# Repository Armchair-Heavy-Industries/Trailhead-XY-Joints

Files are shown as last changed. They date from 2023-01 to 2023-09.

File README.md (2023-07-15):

# Trailhead-XY-Joints
Modified XY joints for the Voron 2.4 and Trident

Project Leads: Corvid and Derpimus

Join me on Discord (https://discord.gg/armchairengineeringsux)
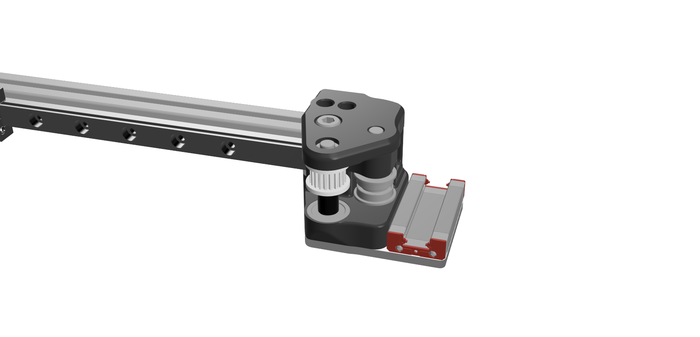
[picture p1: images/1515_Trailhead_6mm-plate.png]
Render

## Note
Consider these files as a beta.

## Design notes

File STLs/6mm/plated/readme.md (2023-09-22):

# Plated 2020 Trailhead assembly

## Bill of materials

| Amount | Part |
| --- | ---- |
| 8 | F695 bearing |
| 2 | De-hubbed pulley or toothed idler |
| 4 | 5x7x1mm shim |
| 4 | 5x35mm G6 steel pins |
| 4 | M3 heatset insert |
| 4 | M5x10 BHCS |
| 2 | M5x35 SHCS |
| 8 | M3x6 BHCS |
| 2 | M3x12 BHCS |
| 4 | M3x16 BHCS |

> [!NOTE]
> It might be useful to design and print spacers between then toothed idler/dehubbed pulley to ensure that the F695 bearings stay in place.

## Assembly view

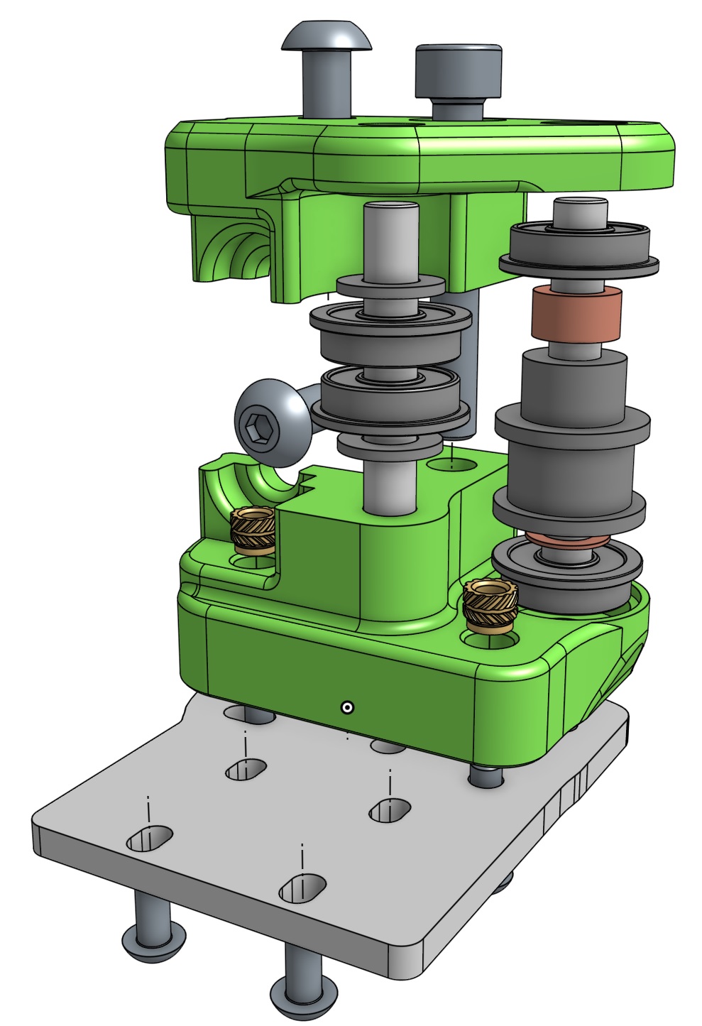
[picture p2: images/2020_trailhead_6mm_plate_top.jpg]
Top perspective


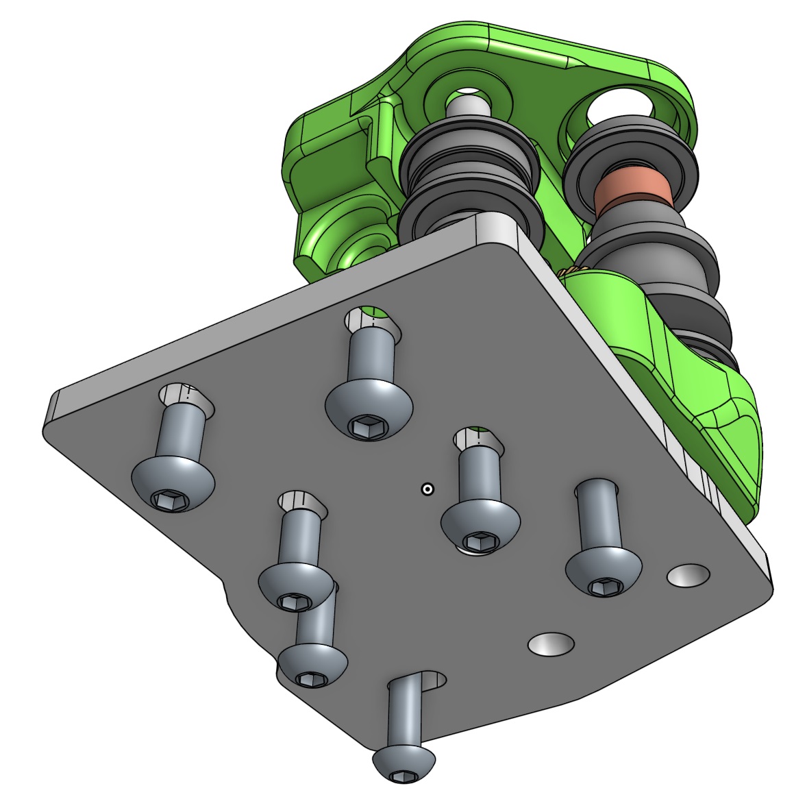
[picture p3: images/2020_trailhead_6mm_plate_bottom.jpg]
Bottom perspective


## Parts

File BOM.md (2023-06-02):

# Bill of Materials

## Plated, 1515 Extrusion, 6mm Belts

### Source:
- 2x cut aluminum plates, 0.125" / 3.2mm thick, using DXF/xyjplate[x2].dxf
- (optional) 1x cut titanium plate, 0.125" / 3.2mm thick, using DXF/1515_x_backer_(size).DXF
- 1515 profile extrusion, e.g. [from Misumi](https://us.misumi-ec.com/vona2/detail/110300465870/)
    - Length is the X-axis extrusion, e.g. 300mm spec Trident uses 380mm extrusion
- M3 tap to use on the extrusion ends

### Print: 
- xyj-left-lower-plated.stl
- xyj-right-lower-plated.stl
- 1515 6mm Trailhead - XY Joint - Left Top.stl
- 1515 6mm Trailhead - XY Joint - Right Top.stl
- 2x misumi1515nodropsquare6mm.stl
- 27x misumi1515nodropsquare.stl (You may have leftovers)

### Small Parts:
- 4x M3 heatset inserts
    - Insert into xyj-*-lower-plated printed parts
- 2x 6mm pulley for belts
- 8x F695 bearing (Four greater than the stock XY joints)
- 27x Roll/Slide-in M3 T-nuts for 1515 Extrusions
    - choose the correct type for your 1515 profile. LDO and Makerbeam are different.
- 29x M3x6mm BHCS
    - 2x through rear of extrusion
    - 10x through X-axis MGN rail (for 300mm spec / 350mm rail / 380mm extrusion)
    - (optional) 9x through titanium backer bar
    - 8x through plates into Y axis MGN carriage
- 4x M3x8mm SHCS
    - 4x through upper printed joints into extrusion
- 4x M3x12mm SHCS
    - 2x through plate, into heatset in lower printed joint
    - 2x into extrusion end
- 2x M3x16mm SHCS
    - 2x through plate, into heatset in lower printed joint
- 2x M3x20mm SHCS
    - 2x through plate, through lower printed joint, into extrusion
- 8x M3 washer
    - 2x for the M3x12 SHCS into the ends of the extrusion
    - 6x for the M3 SHCS screws through bottom of the plates
    - No washers for the M3x6 BHCS screws that go into the carriages
- 2x M5x40mm SHCS
    - 2x through entire XY joint from top to bottom.
- 2x M5 washer
    - 2x between plate and nut
- 2x M5 nut
    - Secure the M5x40mm SHCS at the bottom of each plate. Tighten with a wrench + pliers
- 4x 5mm x 35mm shafts (These are different from the 40mm shafts used in the regular pins mod!)

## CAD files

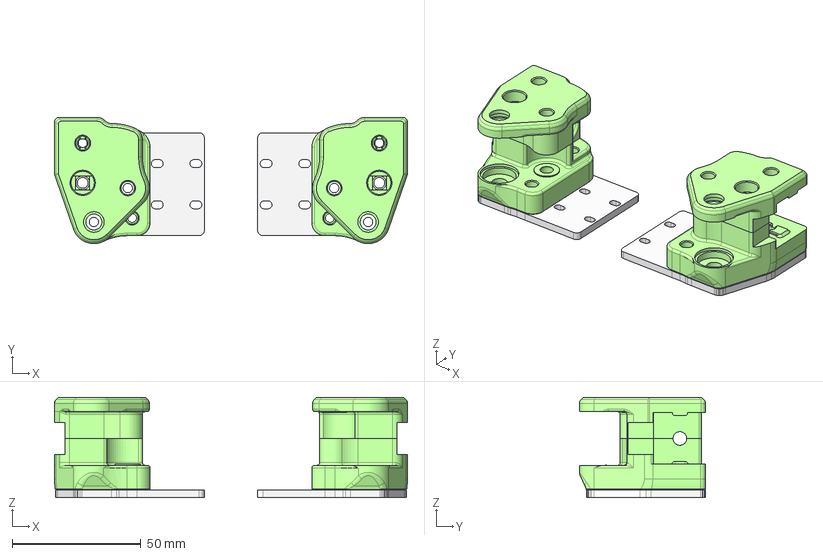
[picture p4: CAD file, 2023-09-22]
CAD/2020_Trailhead_6mm-plate.step
137.1 x 49.0 x 39.0 mm
XY Joint Left Bottom R3
Trailhead Plate x 2
XY Joint Right Bottom R3
XY Joint Left Top R3
XY Joint Right Top R3

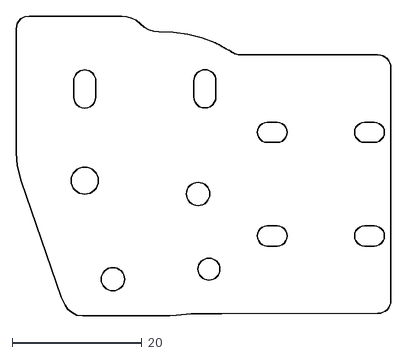
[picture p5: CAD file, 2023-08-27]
DXF/trailhead_plate[x2].dxf
57.8 x 46.3

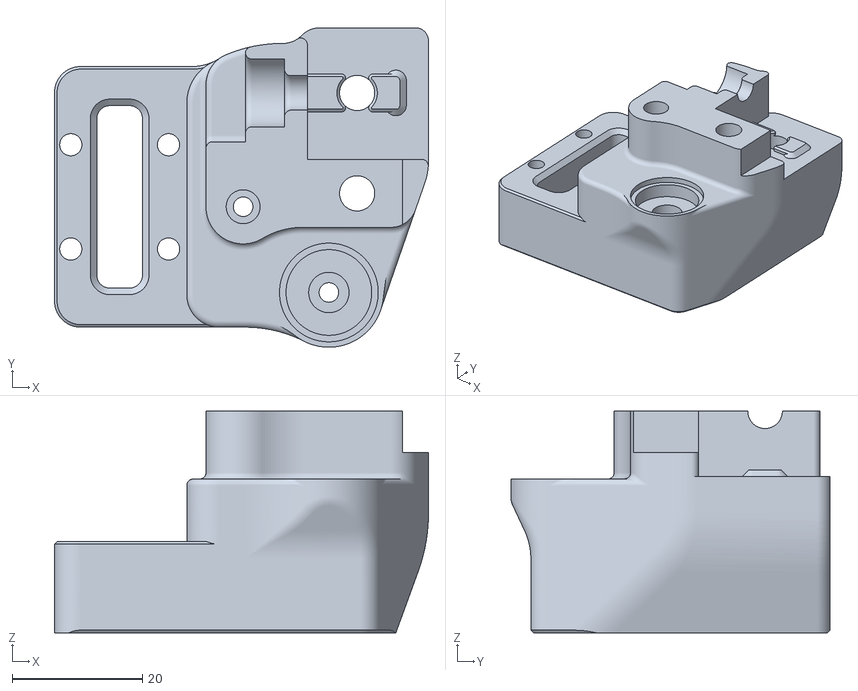
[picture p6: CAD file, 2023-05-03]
STLs/6mm/2020 6mm Trailhead - XY Joint - Left Bottom.stl
57.4 x 49.0 x 34.0

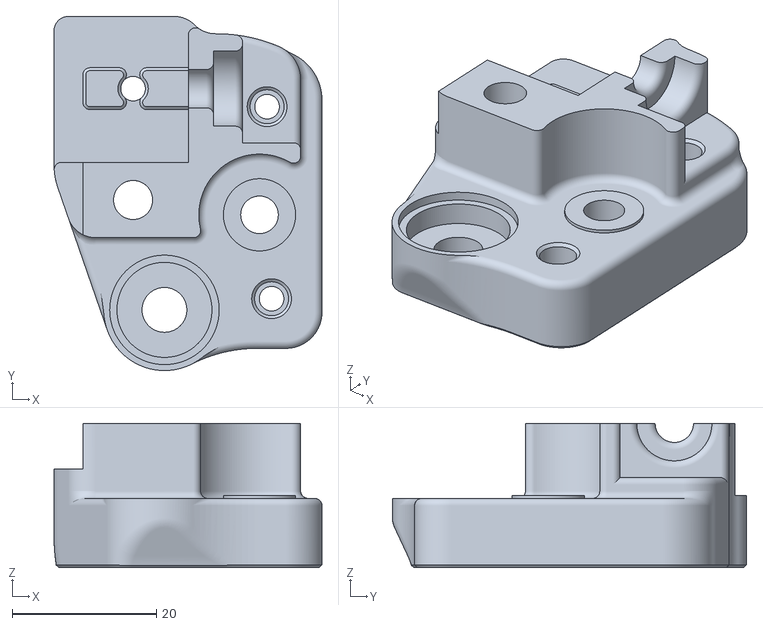
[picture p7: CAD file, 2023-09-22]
STLs/6mm/plated/2020-xyj-right-lower-plated.stl
37.1 x 49.0 x 20.0

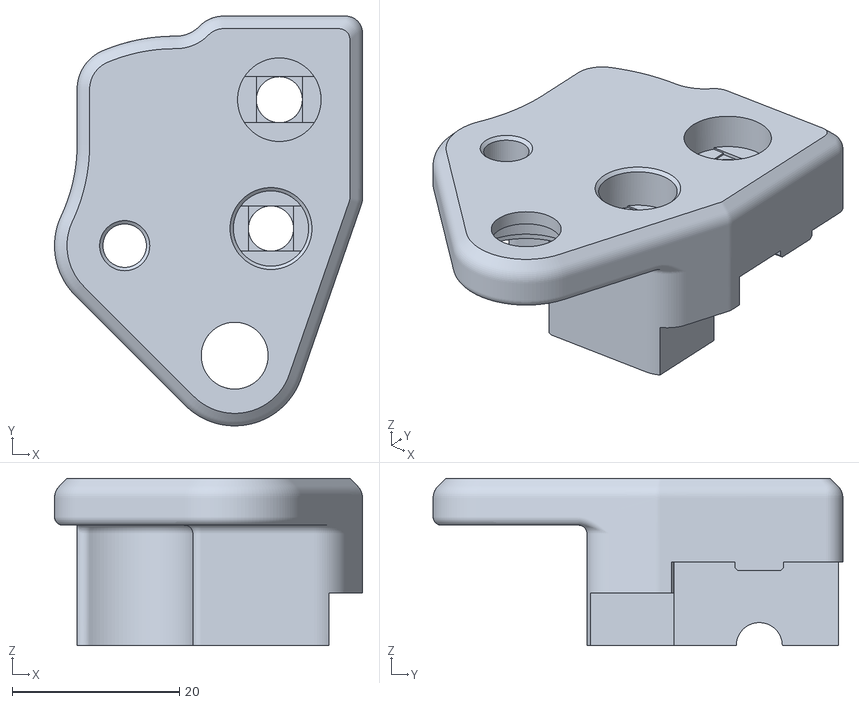
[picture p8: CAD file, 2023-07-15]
STLs/9mm/plated/2020 9mm Trailhead - XY Joint - Left Top - Plated.stl
36.8 x 49.0 x 20.0

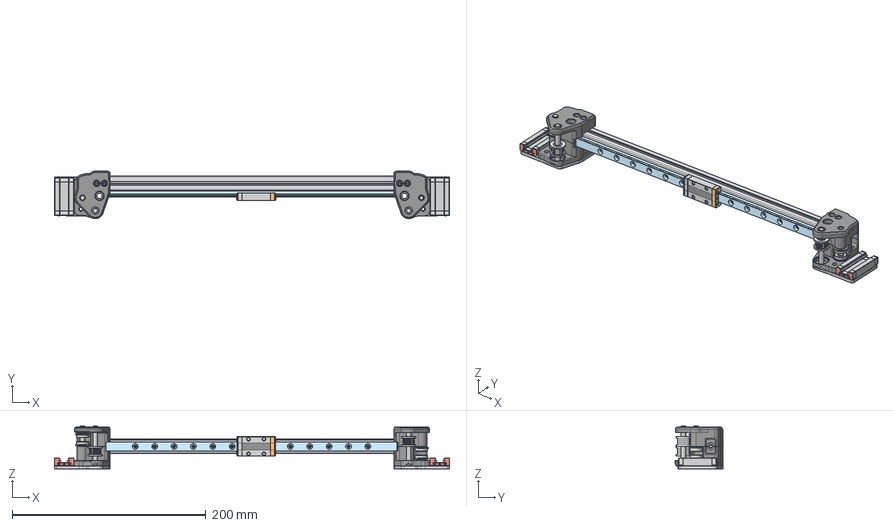
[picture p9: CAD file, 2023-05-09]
CAD/1515_Trailhead_9mm-plate.step
407.6 x 49.0 x 44.2 mm
v1_MGN9_250
MGN9H - Carriage (1) (1)
HFS3-1515-330
5x40 Pin
MGN9H - Carriage (5) (1)
F695 ZZ (1)
GT2 20T Idler Gates v2
5x40 Pin (1)
5x40 Pin (2)
F695 ZZ (1)_1
MGN9H - Carriage (5) (1) (1)
MGN9H - Carriage (9)
XY Joint - Left v3
XY Joint - Right v1
MGN9H - Carriage (4) (1)
GT2 20T Idler Gates v2 (1)
plate (1) (1)
MGN9H - Carriage (1) (1) (1)
M5 1mm Spacer (1)_1
F695 ZZ (1) (1)
MGN9H - Carriage (2) (1)
plate (1)
MGN9H - Carriage (3) (1)
MGN9H - Carriage (4) (1) (1)
MGN9H - Carriage (9) (1)
v1_MGN9-H
id23
MGN9H - Carriage (3) (1) (1)
F695 ZZ (1)_1 (1)
id17
id14
id20
id2
id5
MGN9H - Carriage (6) (1)
MGN9H - Carriage (6) (1) (1)
M5 1mm Spacer (1)_1 (1)
GT2 20T Idler Gates v2 (2)
GT2 20T Idler Gates v2 (3)
MGN9H - Carriage (2) (1) (1)
GT2 20T Idler v3 (2)
M5 1mm Spacer (1)
MGN9H - Carriage (8) (1)
id8
M5 1mm Spacer (1) (1)
GT2 20T Idler v3 (2) (1)
GT2 20T Idler v3 (2) (2)
GT2 20T Idler Gates v2 (4)
GT2 20T Idler Gates v2 (5)
MGN9H - Carriage (7) (1)
MGN9H - Carriage (8) (1) (1)
id11
GT2 20T Idler v3 (2) (3)
MGN9H - Carriage (7) (1) (1)

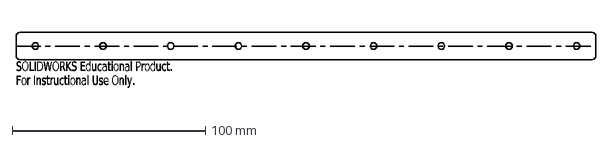
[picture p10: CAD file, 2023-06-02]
DXF/1515_x_backer_300.DXF
SOLIDWORKS Educational Product.
For Instructional Use Only.

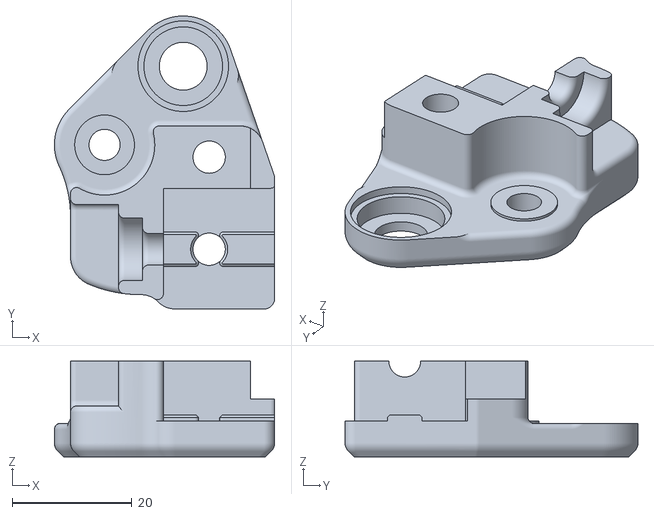
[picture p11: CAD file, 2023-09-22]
STLs/6mm/plated/2020-xyj-left-upper-plated.stl
36.8 x 49.0 x 16.0

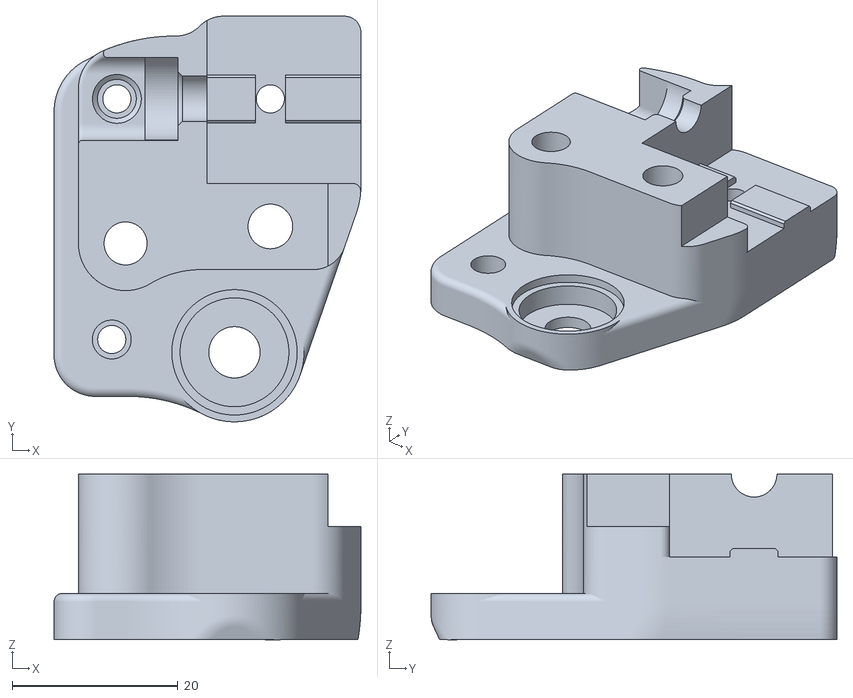
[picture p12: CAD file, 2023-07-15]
STLs/9mm/plated/2020 9mm Trailhead - XY Joint - Left Bottom - Plated.stl
37.1 x 49.0 x 20.0

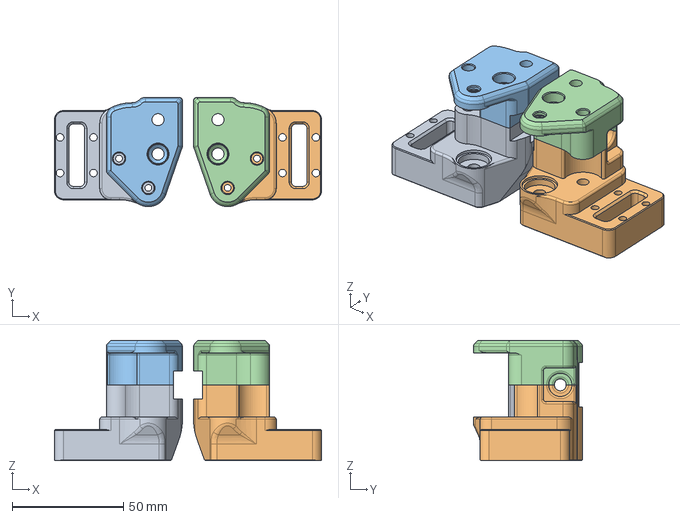
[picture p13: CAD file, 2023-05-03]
CAD/2020_Trailhead_9mm.step
119.8 x 49.0 x 54.0 mm

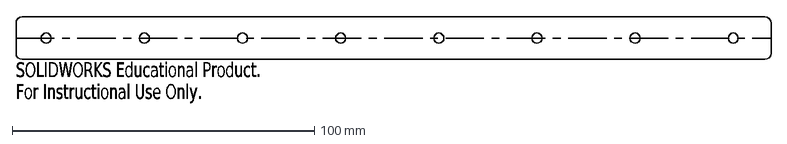
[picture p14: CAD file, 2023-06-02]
DXF/1515_x_backer_250.DXF
SOLIDWORKS Educational Product.
For Instructional Use Only.

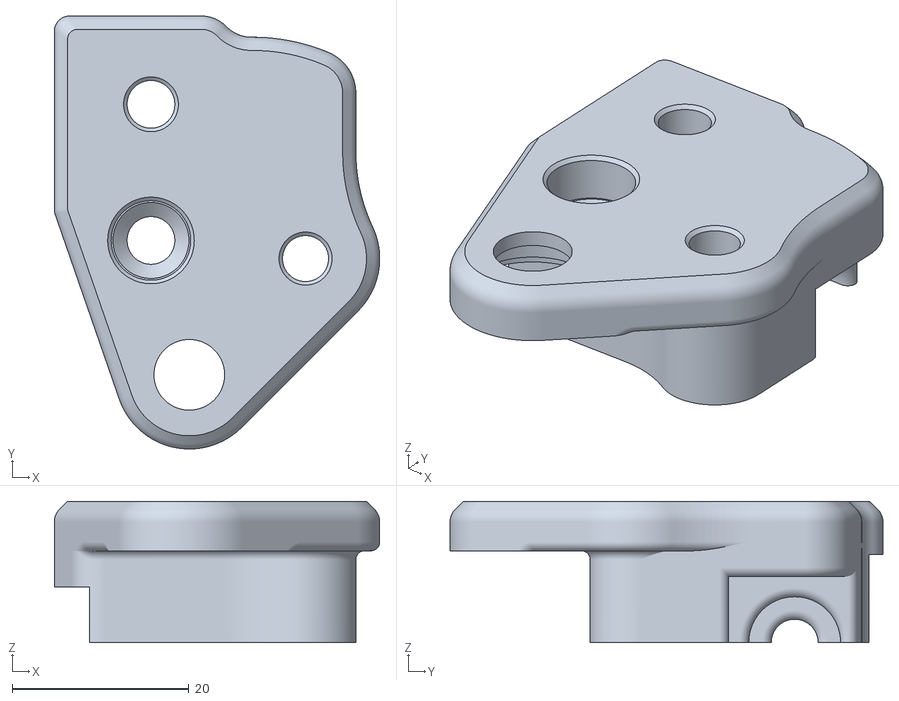
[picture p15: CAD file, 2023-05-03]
STLs/6mm/2020 6mm Trailhead - XY Joint - Right Top.stl
36.8 x 49.0 x 16.0

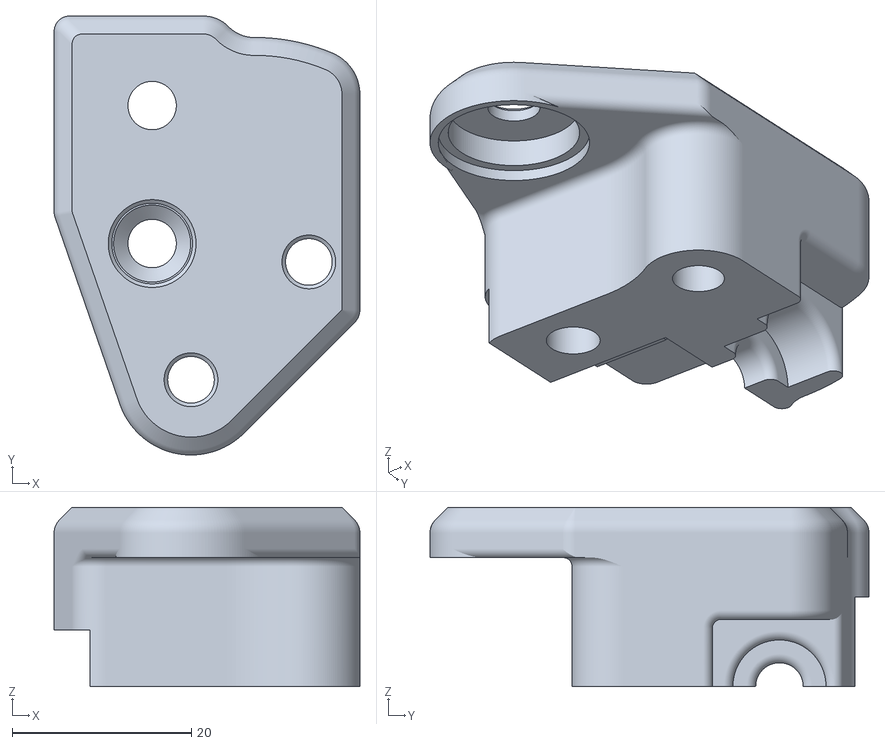
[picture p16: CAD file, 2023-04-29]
STLs/9mm/2020 9mm Trailhead - XY Joint - Right Top.stl
34.2 x 49.0 x 20.0

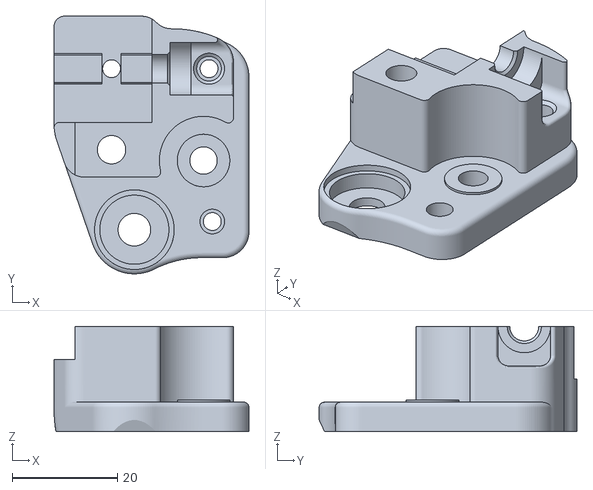
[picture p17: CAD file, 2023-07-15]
STLs/9mm/plated/2020 9mm Trailhead - XY Joint - Right Bottom - Plated.stl
37.1 x 49.0 x 20.0

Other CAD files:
STLs/9mm/2020 9mm Trailhead - XY Joint - Left Bottom.stl
STLs/6mm/2020 6mm Trailhead - XY Joint - Right Bottom.stl
STLs/9mm/2020 9mm Trailhead - XY Joint - Right Bottom.stl
STLs/6mm/plated/2020-xyj-left-lower-plated.stl
CAD/1515_Trailhead_6mm-plate.step
CAD/1515_Trailhead_6mm.step
CAD/2020_Trailhead_6mm.step
STLs/6mm/1515 6mm Trailhead - XY Joint - Left Bottom.stl
STLs/6mm/1515 6mm Trailhead - XY Joint - Left Top.stl
STLs/6mm/1515 6mm Trailhead - XY Joint - Right Bottom.stl
STLs/6mm/1515 6mm Trailhead - XY Joint - Right Top.stl
STLs/6mm/2020 6mm Trailhead - XY Joint - Left Top.stl
STLs/6mm/plated/1515-xyj-left-lower-plated.stl
STLs/6mm/plated/1515-xyj-right-lower-plated.stl
STLs/6mm/plated/2020-xyj-right-upper-plated.stl
STLs/9mm/2020 9mm Trailhead - XY Joint - Left Top.stl
STLs/9mm/plated/2020 9mm Trailhead - XY Joint - Right Top - Plated.stl
STLs/misumi1515nodropsquare.stl
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

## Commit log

2023-01-05 Create CAD
2023-01-15 Create 6mm
2023-04-29 Adding CAD
    [1515_Trailhead_6mm_v3.step, 2020_Trailhead_6mm.step, 2020_Trailhead_9mm.step]
2023-04-29 Update STLs
    [1515 6mm Trailhead - XY Joint - Left Bottom.stl, 1515 6mm Trailhead - XY Joint - Left Top.stl, 1515 6mm Trailhead - XY Joint - Right Bottom.stl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]
2023-04-30 i fucked up. sorry
    [1515_Trailhead_6mm.step]
2023-05-03 Fixed bearing fitment on 6mm 2020
    [2020 6mm Trailhead - XY Joint - Left Bottom.stl, 2020 6mm Trailhead - XY Joint - Right Bottom.stl, 2020 6mm Trailhead - XY Joint - Right Top.stl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]
2023-05-03 Fix bearing fitment on 9mm
    [2020 9mm Trailhead - XY Joint - Left Bottom.stl, 2020 9mm Trailhead - XY Joint - Right Bottom.stl, 2020_Trailhead_9mm.step]
2023-05-31 Add BOM
2023-06-02 Add titanium backer DXFs and update BOM
    [1515_x_backer_250.DXF, 1515_x_backer_300.DXF, xyjplate[x2].dxf]
2023-06-02 Update BOM for titanium backer
    [xyjplate[x2].dxf]
2023-07-14 Add files via upload
    added universal trailhead plate. this will work for 2020 and 1515. I also added slots for the Y rail bolts to help with deracking. The other set of holes is to allow use of 1515 or 2020
    [trailhead_plate[x2].dxf]
2023-07-14 fixed the god darn file names
    [2020 9mm Trailhead - XY Joint - Left Bottom - Plated.stl, 2020 9mm Trailhead - XY Joint - Left Top - Plated.stl, 2020 9mm Trailhead - XY Joint - Right Bottom -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]
2023-07-15 fucked up the extrusion index thingies. sorry
    [2020 9mm Trailhead - XY Joint - Left Bottom - Plated.stl, 2020 9mm Trailhead - XY Joint - Left Top - Plated.stl, 2020 9mm Trailhead - XY Joint - Right Bottom -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]
2023-09-22 Added 6mm plated 2020 version
    Renamed assembly.md to readme.md
    Updated image path
    [2020-xyj-left-lower-plated.stl, 2020-xyj-left-upper-plated.stl, 2020-xyj-right-lower-plated.stl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]
